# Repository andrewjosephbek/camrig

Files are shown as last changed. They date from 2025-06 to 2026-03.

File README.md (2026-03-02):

# Motorized Camera Tracking Rig

This project implements a compact Camera Motion Platform; integrating custom electronics, embedded firmware, and low-backlash mechanical design. Version 2 is currently in progress (UI firmware is finished, PCB Layout is finished, housing IP)! V1 KiCAD files are for an old version, may be incomplete. 

---

## Version 1: Demo
[Overview Video](https://youtu.be/gTk2HjM0wyA) (1:53)

---

## Version 2: PCB

### 3D:
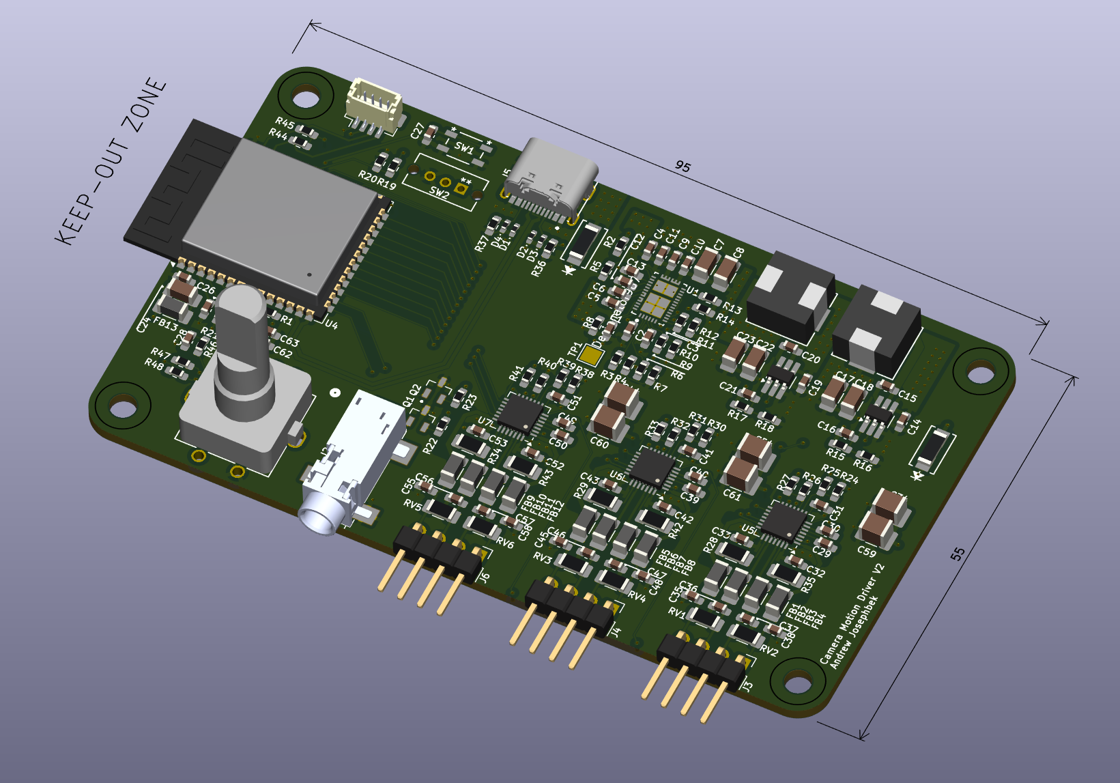
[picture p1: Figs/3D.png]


### Layer 1 (Signal):
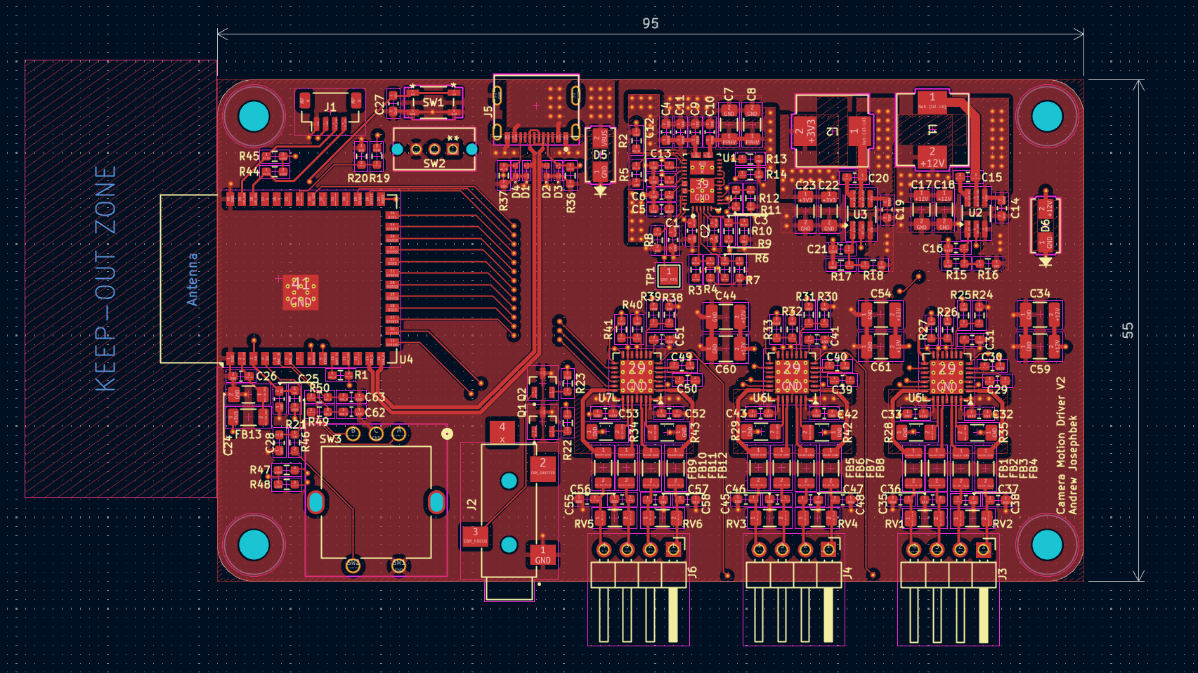
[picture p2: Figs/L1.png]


### Layer 2 (Ground):
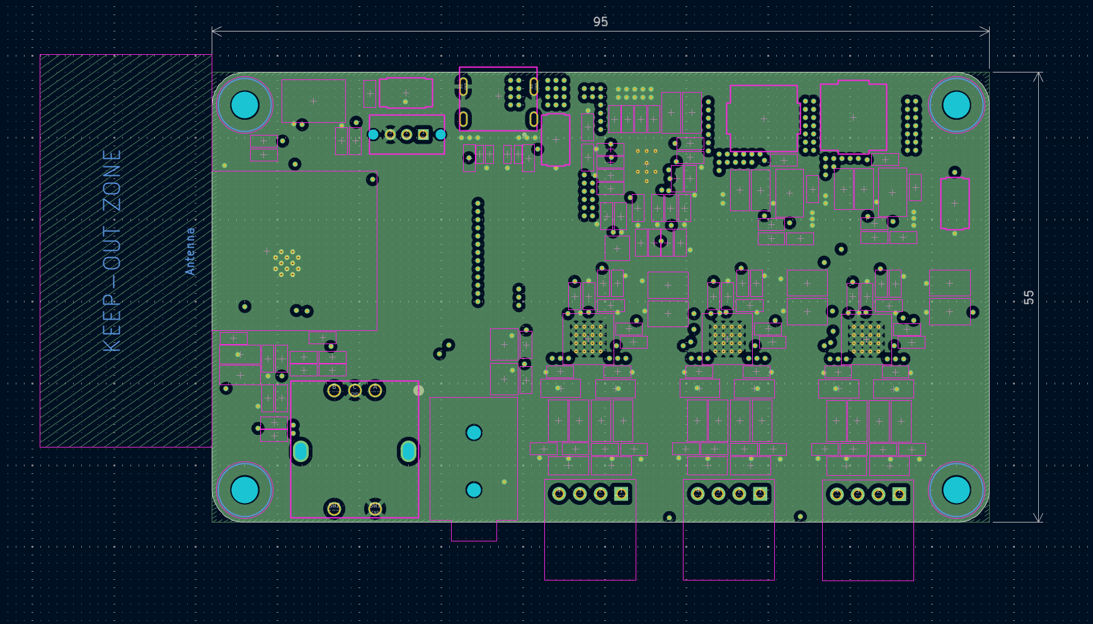
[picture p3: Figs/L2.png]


### Layer 3 (Power):
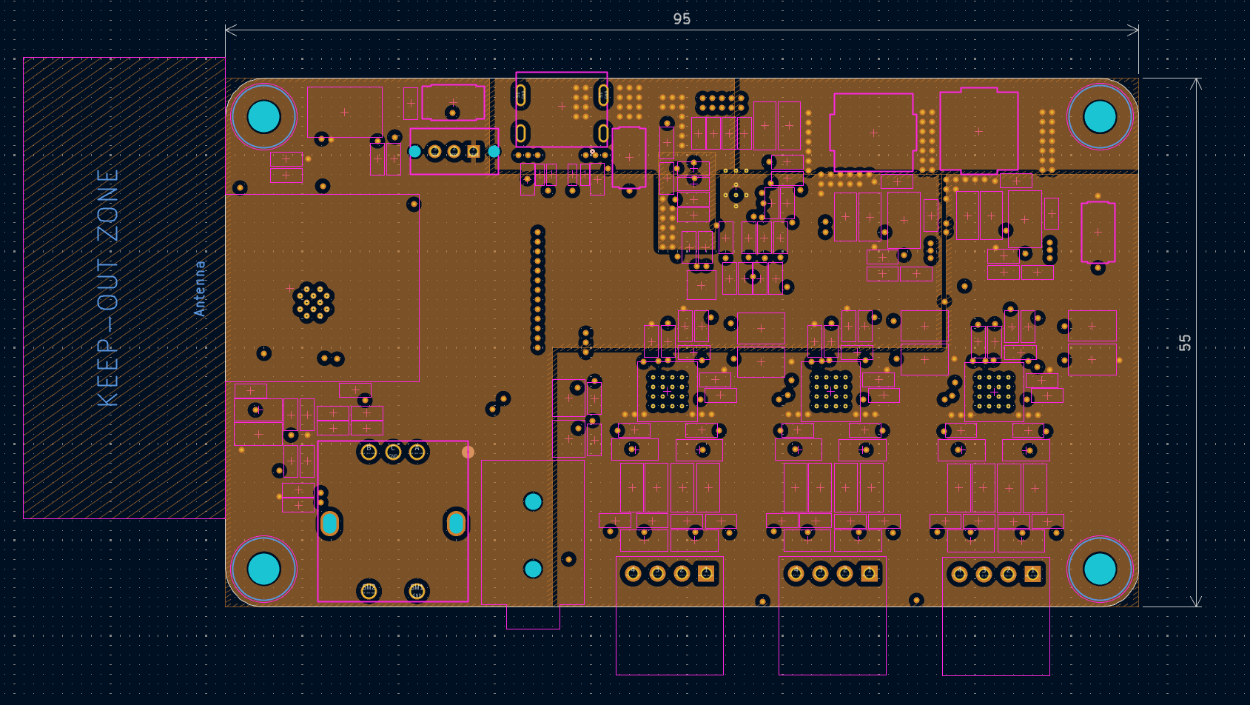
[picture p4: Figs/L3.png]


### Layer 4 (Signal):
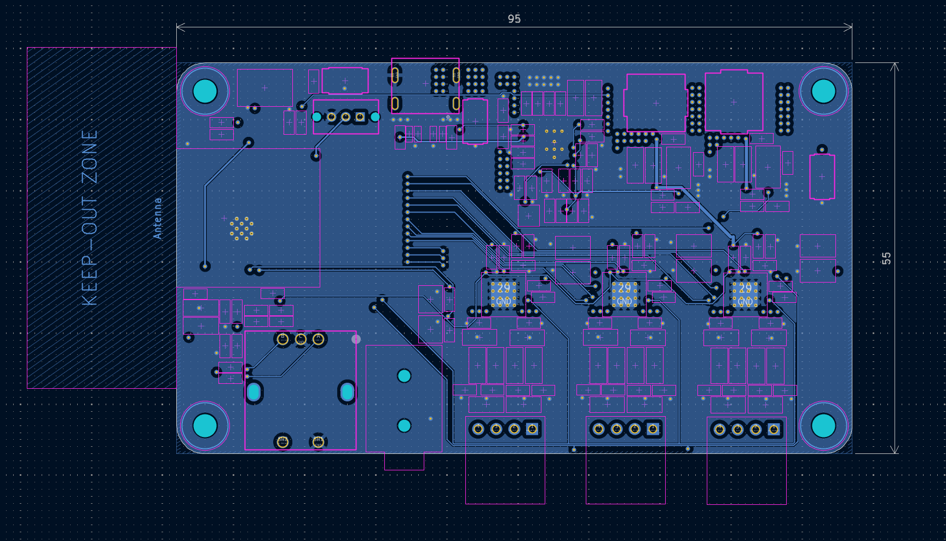
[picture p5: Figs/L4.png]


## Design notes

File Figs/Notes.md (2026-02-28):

https://espressif.github.io/esp32-c3-book-en/chapter_5/5.3/5.3.5.html

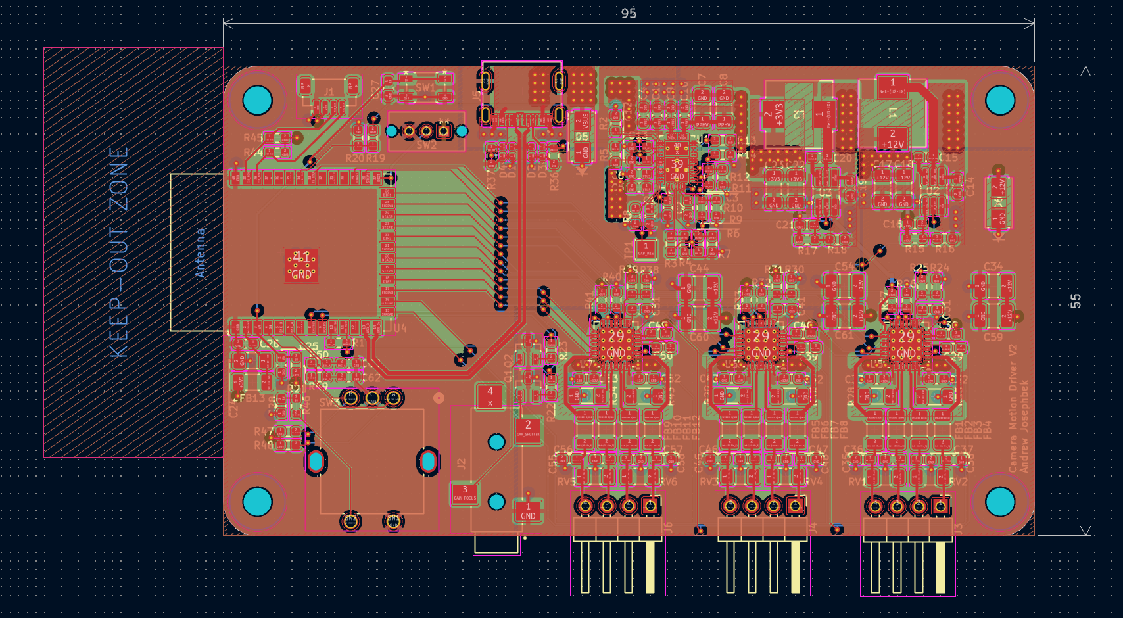
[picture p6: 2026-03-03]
Figs/All Layers.png

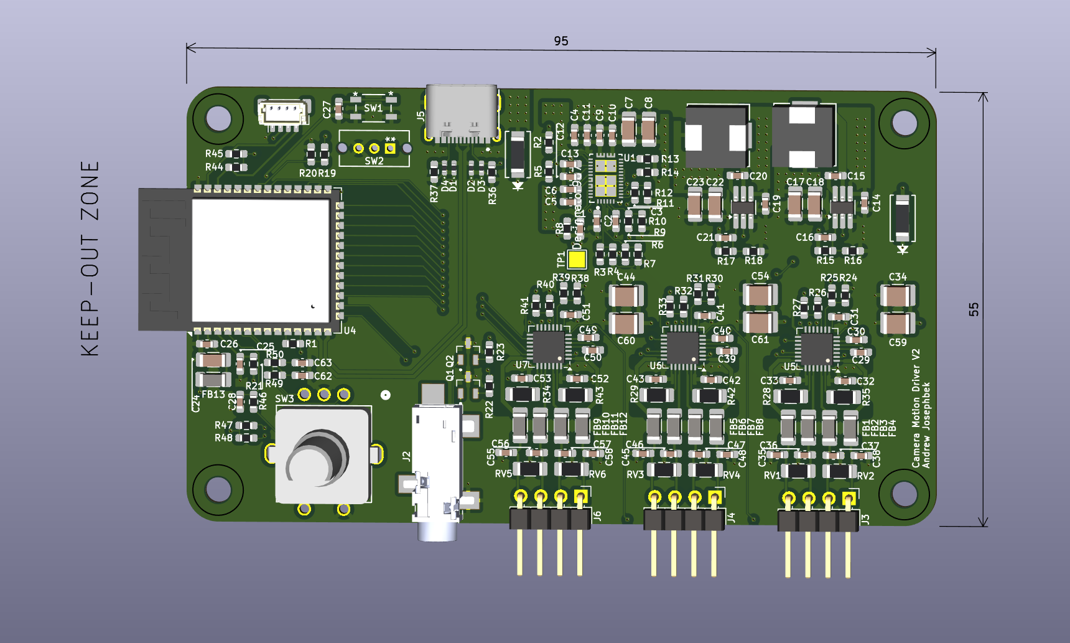
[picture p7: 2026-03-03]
Figs/3D ortho.png

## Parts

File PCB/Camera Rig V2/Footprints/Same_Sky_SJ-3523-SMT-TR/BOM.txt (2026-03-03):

3DX_Same_Sky_Supplier: Same Sky
3DX_Same_Sky_Description: 3.5 mm, Stereo, Right Angle, Surface Mount (SMT), 3 Conductors, 0 Internal Switches, Audio Jack Connector
3DX_Same_Sky_Model Number: SJ-3523-SMT-TR

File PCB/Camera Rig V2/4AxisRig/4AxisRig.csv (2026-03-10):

Reference | Value | Footprint | Part Number | Datasheet | Link | Qty | Description_1
Q1,Q2 | NMOS | 2N7000:SOT95P240X111-3N | 2N7002K | https://www.onsemi.com/download/data-sheet/pdf/2n7002k-d.pdf |  | 2
C1,C2,C10,C14,C19 | 10uF | Capacitor_SMD:C_0603_1608Metric_Pad1.08x0.95mm_HandSolder |  | ~ |  | 5
C3,C4 | 4.7uF | Capacitor_SMD:C_0603_1608Metric_Pad1.08x0.95mm_HandSolder |  | ~ |  | 2
C5,C6,C9,C11 | 0.01uF | Capacitor_SMD:C_0603_1608Metric_Pad1.08x0.95mm_HandSolder |  | ~ |  | 4
C12,C13 | 330pF | Capacitor_SMD:C_0603_1608Metric_Pad1.08x0.95mm_HandSolder |  | ~ |  | 2
C15,C20,C26,C27,C28,C32,C33,C35,C36,C37,C38,C42,C43,C45,C46,C47,C48,C52,C53,C55,C56,C57,C58,C62,C63 | 100nF | Capacitor_SMD:C_0603_1608Metric_Pad1.08x0.95mm_HandSolder |  | ~ |  | 25
C16,C21 | 47pF | Capacitor_SMD:C_0603_1608Metric_Pad1.08x0.95mm_HandSolder |  | ~ |  | 2
C25 | 1uF | Capacitor_SMD:C_0603_1608Metric_Pad1.08x0.95mm_HandSolder |  | ~ |  | 1
C29,C39,C49 | 100nF 16V | Capacitor_SMD:C_0603_1608Metric_Pad1.08x0.95mm_HandSolder |  | ~ |  | 3
C30,C40,C50 | 22nF 50V | Capacitor_SMD:C_0603_1608Metric_Pad1.08x0.95mm_HandSolder |  | ~ |  | 3
C31,C41,C51 | 2.2uF 6.3V | Capacitor_SMD:C_0603_1608Metric_Pad1.08x0.95mm_HandSolder |  | ~ |  | 3
C7,C8,C17,C18,C22,C23,C24 | 22uF | Capacitor_SMD:C_1206_3216Metric_Pad1.33x1.80mm_HandSolder |  | https://mm.digikey.com/Volume0/opasdata/d220001/medias/docus/506/TMK316BBJ226ML-T_SS.pdf |  | 7
C34,C44,C54,C59,C60,C61 | 47uF | Capacitor_SMD:C_1210_3225Metric_Pad1.33x2.70mm_HandSolder |  | https://www.digikey.com/en/products/detail/murata-electronics/GRM32EC81C476KE15L/5027615 |  | 6
J1 | Conn_01x05_Socket | Connector_JST:JST_SH_BM04B-SRSS-TB_1x04-1MP_P1.00mm_Vertical |  | ~ |  | 1
J3,J4,J6 | Motor Connector | Connector_PinHeader_2.54mm:PinHeader_1x04_P2.54mm_Horizontal |  | ~ |  | 3
D1,D2,D3,D4 | ESD441 | Diode_SMD:D_0402_1005Metric_Pad0.77x0.64mm_HandSolder |  | https://www.ti.com/lit/ds/symlink/esd441.pdf?ts=1772263166249 |  | 4
D5 | T4F10A | Diode_SMD:Nexperia_CFP3_SOD-123W |  | DF2B7AFS |  | 1
L2 | 15uH | DR74-150-R:DR74 | DR74-150-R | https://www.eaton.com/content/dam/eaton/products/electronic-components/resources/data-sheet/eaton-dr-high-power-density-high-efficiency-shielded-drum-core-pow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 |  | 1
L1 | 4.7uH | DR74-4R7-R:DR74 | DR74-4R7-R | https://www.eaton.com/content/dam/eaton/products/electronic-components/resources/data-sheet/eaton-dr-high-power-density-high-efficiency-shielded-drum-core-pow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 |  | 1
FB1,FB2,FB3,FB4,FB5,FB6,FB7,FB8,FB9,FB10,FB11,FB12 | 2512065007Y6 | Inductor_SMD:L_1206_3216Metric_Pad1.22x1.90mm_HandSolder |  | https://fair-rite.com/print_product.php?pid=33593 |  | 12
H1,H2,H3,H4 | MountingHole | MountingHole:MountingHole_3.2mm_M3 |  | ~ |  | 4
U5,U6,U7 | TMC2209-LA | Package_DFN_QFN:VQFN-28-1EP_5x5mm_P0.5mm_EP3.7x3.7mm_ThermalVias | TMC2209-LA | https://www.analog.com/media/en/technical-documentation/data-sheets/TMC2209_datasheet_rev1.09.pdf |  | 3
U2,U3 | AN_SY8105 | Package_TO_SOT_SMD:TSOT-23-6_HandSoldering | AN_SY8105 |  |  | 2
SW3 | PEC11L-4120F-S0020 | PEC11L-4120F-S0020:PEC11L-4x20F-Sxxx_BRN |  | PEC11L-4120F-S0020 |  | 1
SW1 | PTS810SJS250SMTRLFS | PTS810SJS250SMTR:SMT_MTRLFS_CNK |  | https://www.ckswitches.com/media/1476/pts810.pdf |  | 1
R1 | 1k | Resistor_SMD:R_0603_1608Metric_Pad0.98x0.95mm_HandSolder |  | ~ |  | 1
R2,R5,R8,R12,R21,R22,R23,R24,R25,R26,R27,R30,R31,R32,R33,R38,R39,R40,R41,R46,R47,R48,R49,R50 | 10k | Resistor_SMD:R_0603_1608Metric_Pad0.98x0.95mm_HandSolder |  | ~ |  | 24
R3,R9,R11 | 191k | Resistor_SMD:R_0603_1608Metric_Pad0.98x0.95mm_HandSolder |  | ~ |  | 3
R4,R10 | 2.5k | Resistor_SMD:R_0603_1608Metric_Pad0.98x0.95mm_HandSolder |  | ~ |  | 2
R6,R7,R17,R19 | 100k | Resistor_SMD:R_0603_1608Metric_Pad0.98x0.95mm_HandSolder |  | ~ |  | 4
R15 | 200k | Resistor_SMD:R_0603_1608Metric_Pad0.98x0.95mm_HandSolder |  | ~ |  | 1
R16 | 10.5k | Resistor_SMD:R_0603_1608Metric_Pad0.98x0.95mm_HandSolder |  | ~ |  | 1
R18 | 22.1k | Resistor_SMD:R_0603_1608Metric_Pad0.98x0.95mm_HandSolder |  | ~ |  | 1
R20 | 19k | Resistor_SMD:R_0603_1608Metric_Pad0.98x0.95mm_HandSolder |  | ~ |  | 1
R36,R37 | 5.1k+-10% | Resistor_SMD:R_0603_1608Metric_Pad0.98x0.95mm_HandSolder |  | ~ |  | 2
R44,R45 | 4.7k | Resistor_SMD:R_0603_1608Metric_Pad0.98x0.95mm_HandSolder |  | ~ |  | 2
R28,R29,R34,R35,R42,R43 | 0.68 | Resistor_SMD:R_1206_3216Metric_Pad1.30x1.75mm_HandSolder |  | ~ |  | 6
RV1,RV2,RV3,RV4,RV5,RV6 | CG0603MLA-18KE | Resistor_SMD:R_1206_3216Metric_Pad1.30x1.75mm_HandSolder |  | ~ |  | 6
U4 | ESP32-S3-WROOM-1 | RF_Module:ESP32-S3-WROOM-1 | ESP32-S3-WROOM-1 | https://www.espressif.com/sites/default/files/documentation/esp32-s3-wroom-1_wroom-1u_datasheet_en.pdf |  | 1
J2 | SJ-3524-SMT | SJ-3524-SMT:CUI_SJ-3524-SMT |  | https://www.sameskydevices.com/product/resource/sj-352x-smt.pdf |  | 1 | 3.5 mm, Stereo, Right Angle, Surface Mount (SMT), 3 Conductors, 1 Internal Switch, Audio Jack Connector
SW2 | SW_SPDT | SS-12D07-VG 4 NS GA PA:SS12D07_CNK |  | https://mm.digikey.com/Volume0/opasdata/d220001/medias/docus/580/SS-12D07-VG_GA_PA.pdf |  | 1
TP7 | TestPoint | TestPoint:TestPoint_Keystone_5000-5004_Miniature |  | ~ |  | 1
TP1,TP2,TP3,TP4,TP5,TP6,TP8 | TestPoint | TestPoint:TestPoint_Pad_1.0x1.0mm |  | ~ |  | 7
U1 | TPS25730DREFR | TPS25730DREFR:REF0038A-MFG | TPS25730DREFR | https://www.ti.com/lit/gpn/tps25730 |  | 1
J5 | USB_C_Receptacle_USB2.0_16P | USB_C_Receptacle_USB2.0_14P:CONN_8p94X6p5X3p16_12L_GCC |  | https://www.usb.org/sites/default/files/documents/usb_type-c.zip |  | 1

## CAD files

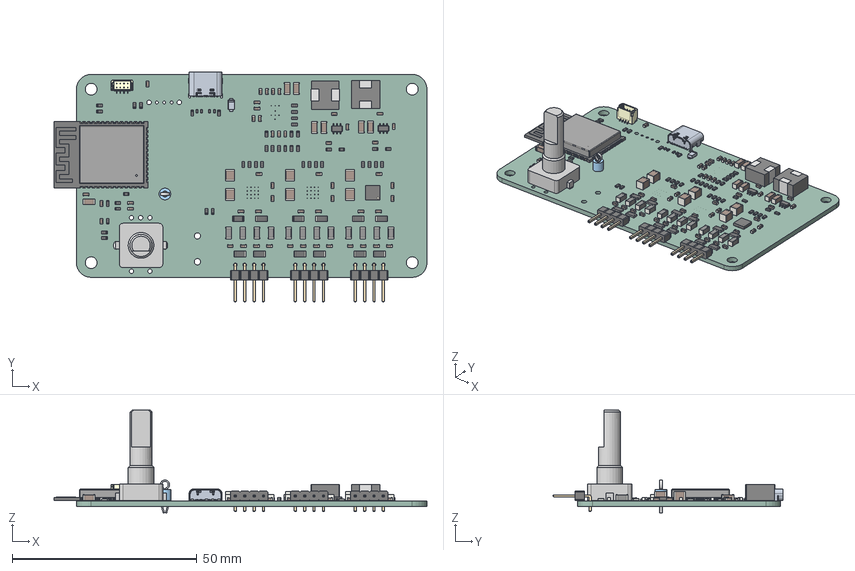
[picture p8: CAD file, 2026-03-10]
PCB/Camera Rig V2/4AxisRig/4AxisRig.step
101.1 x 62.3 x 27.8 mm
C_1210_3225Metric x 6
L_1206_3216Metric x 12
C_0603_1608Metric x 50
C_1206_3216Metric x 7
R_0402_1005Metric x 4
R_0603_1608Metric x 44
R_1206_3216Metric x 12
TestPoint_Keystone_5005-5009_Compact
4AxisRig 1.28.1
DR74 x 2
QFN-32-1EP_4x4mm_P0.4mm_EP2.65x2.65mm
PinHeader_1x04_P2.54mm_Horizontal x 3
TSOT-23-6 x 2
BM04B-SRSS-TB--3DModel-STEP-1
Rot Enc v1
ESP32-S3-WROOM-1
4AxisRig_PCB

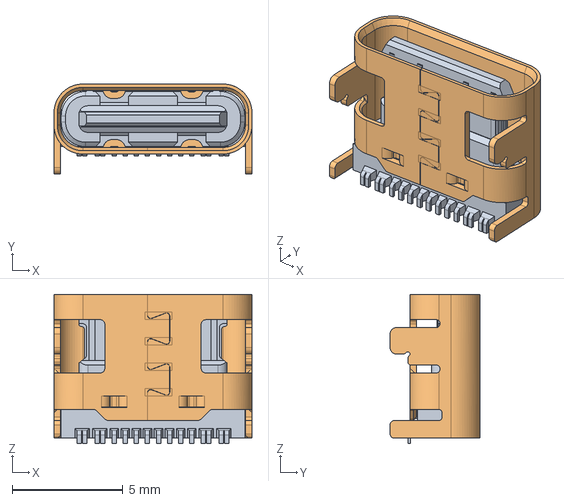
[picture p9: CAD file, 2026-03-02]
PCB/Camera Rig V2/Footprints/179536900-3-usb4215-03-a/usb4215-03-a.stp
8.94 x 4.06 x 6.75 mm

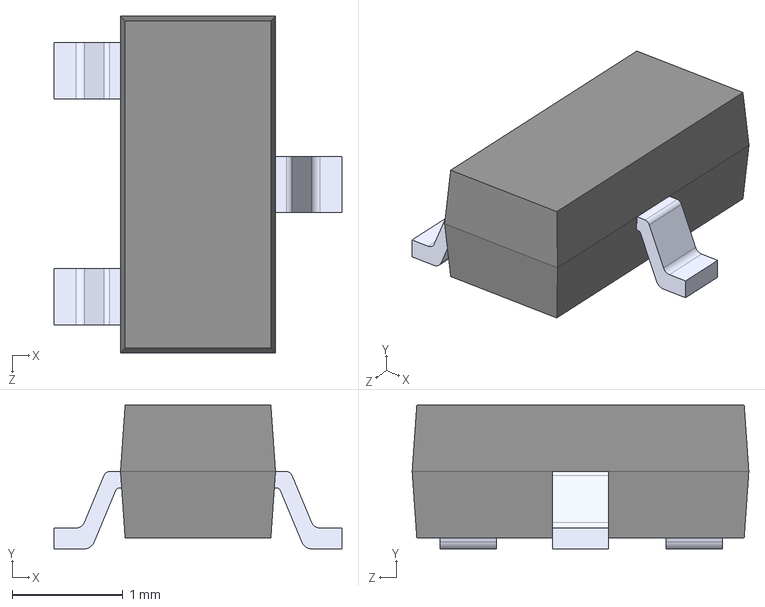
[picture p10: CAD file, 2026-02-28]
PCB/Camera Rig V2/Footprints/2N7002KT7G/2N7002KT7G.step
2.60 x 1.30 x 3.04 mm

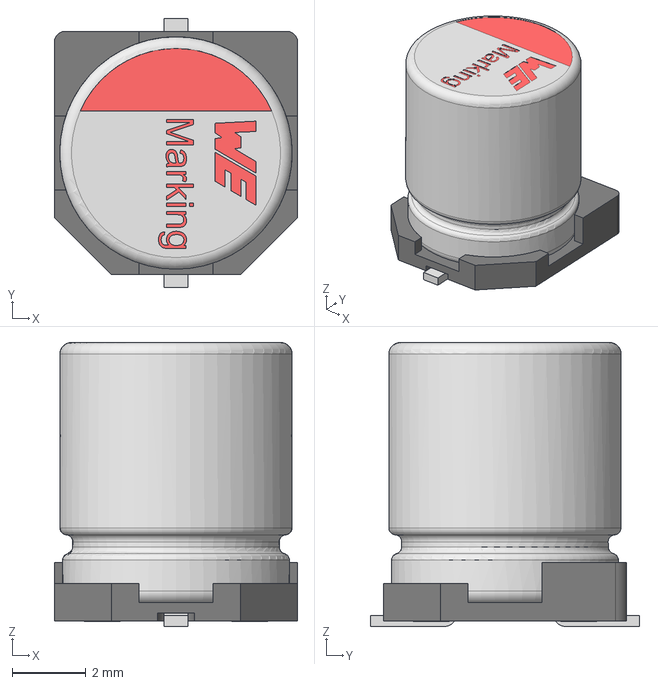
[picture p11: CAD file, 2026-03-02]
PCB/Camera Rig V2/Footprints/Download_STP_86508xx450xx+(rev1)/Download_STP_86508xx450xx+%28rev1%29.stp
6.60 x 7.30 x 7.70 mm
capicitor_6.3x7.7x2.2
Base_Φ6_3Capacitor

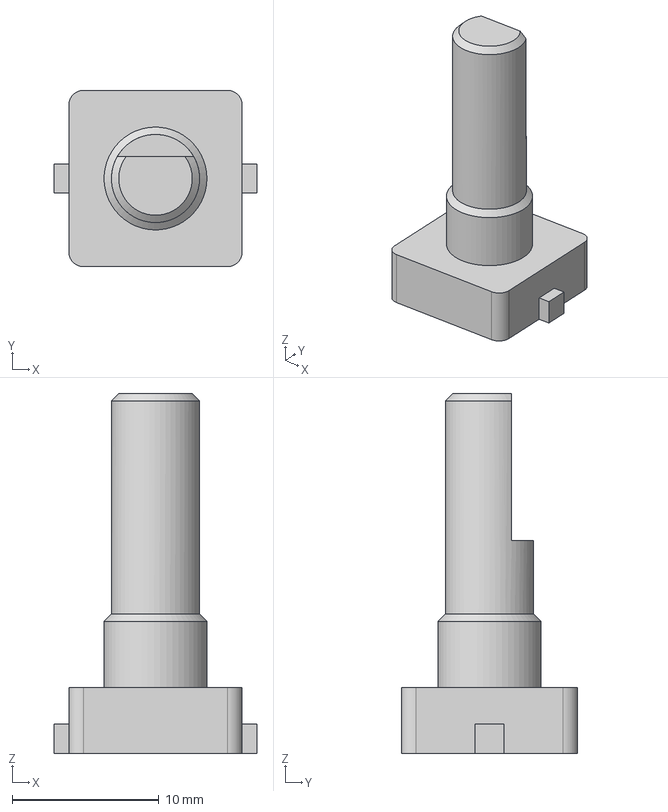
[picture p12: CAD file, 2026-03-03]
PCB/Camera Rig V2/Footprints/Rot Enc v1.step
13.8 x 12.0 x 24.5 mm

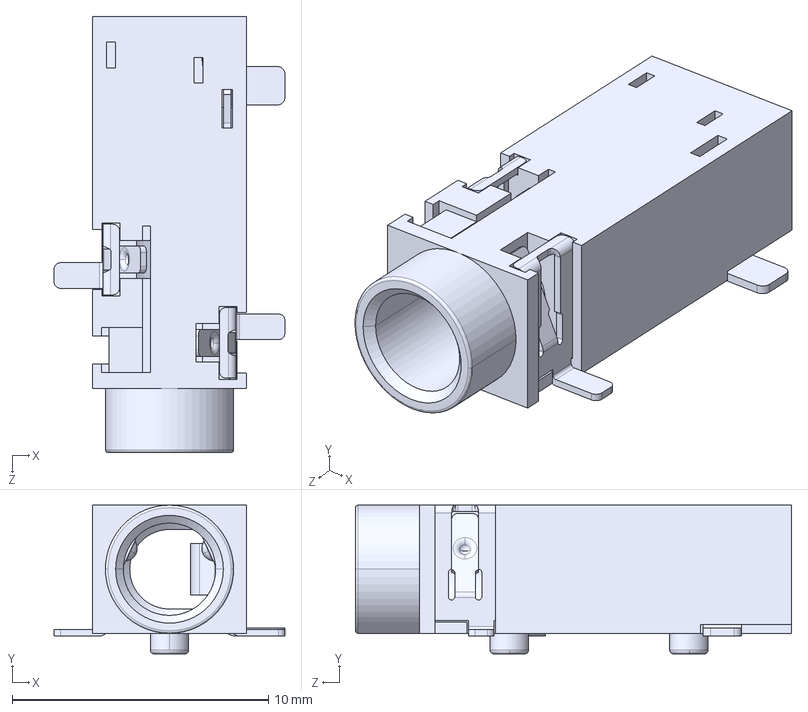
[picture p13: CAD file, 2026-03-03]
PCB/Camera Rig V2/Footprints/Same_Sky_SJ-3523-SMT-TR/Same_Sky_SJ-3523-SMT-TR.step
9.00 x 5.80 x 17.0 mm

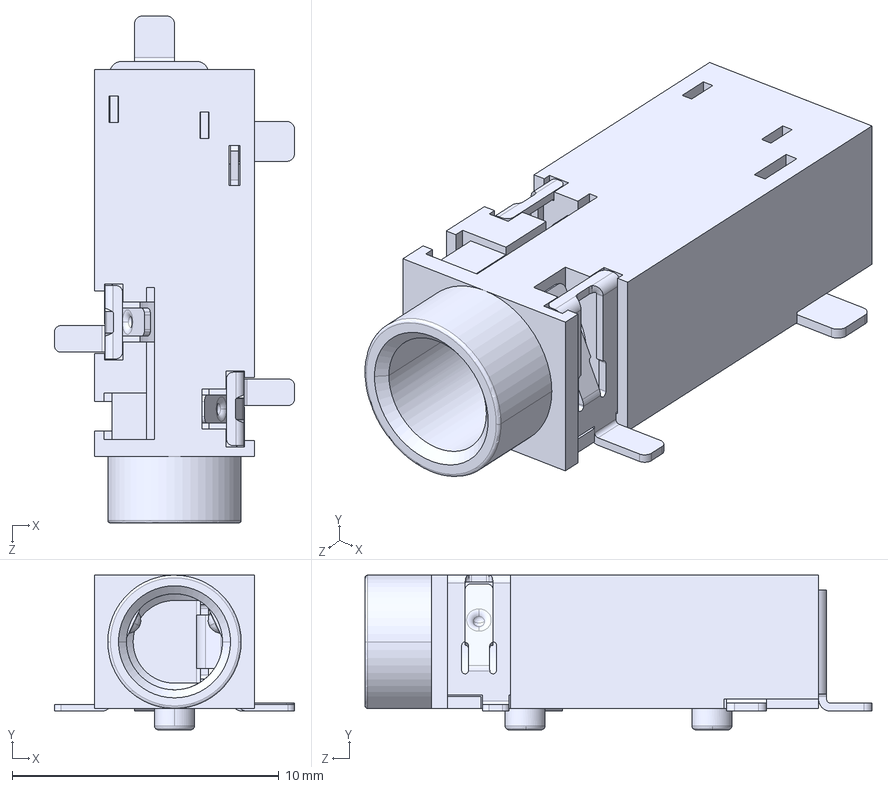
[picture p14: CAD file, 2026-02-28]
PCB/Camera Rig V2/Footprints/SJ-3524-SMT/SJ-3524-SMT.step
9.00 x 5.80 x 19.0 mm

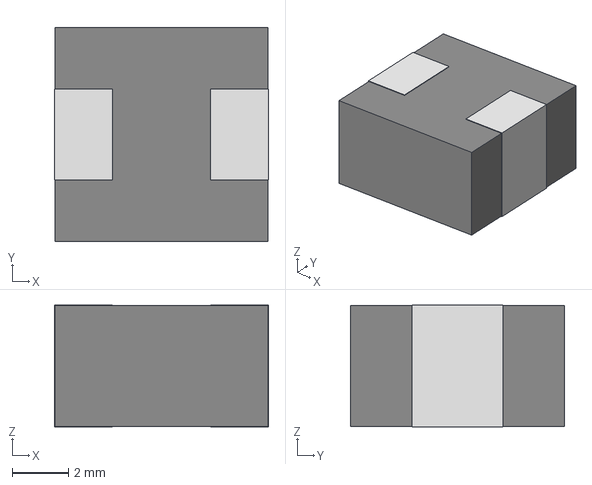
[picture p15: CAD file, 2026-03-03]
PCB/Camera Rig V2/Footprints/ul_DR74-150-R (1)/DR74.step
7.62 x 7.62 x 4.34 mm

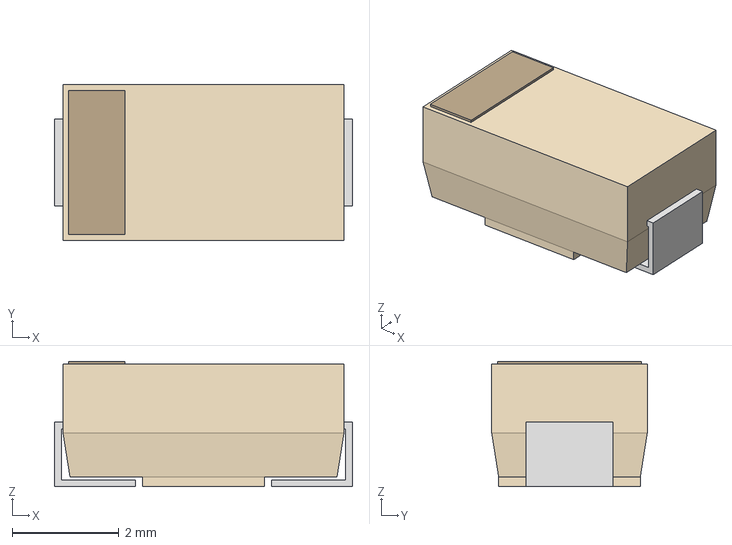
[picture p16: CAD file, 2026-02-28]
PCB/Camera Rig V2/Footprints/ul_SMAJ10CA-13-F/SMA_DIO.step
5.59 x 2.92 x 2.35 mm

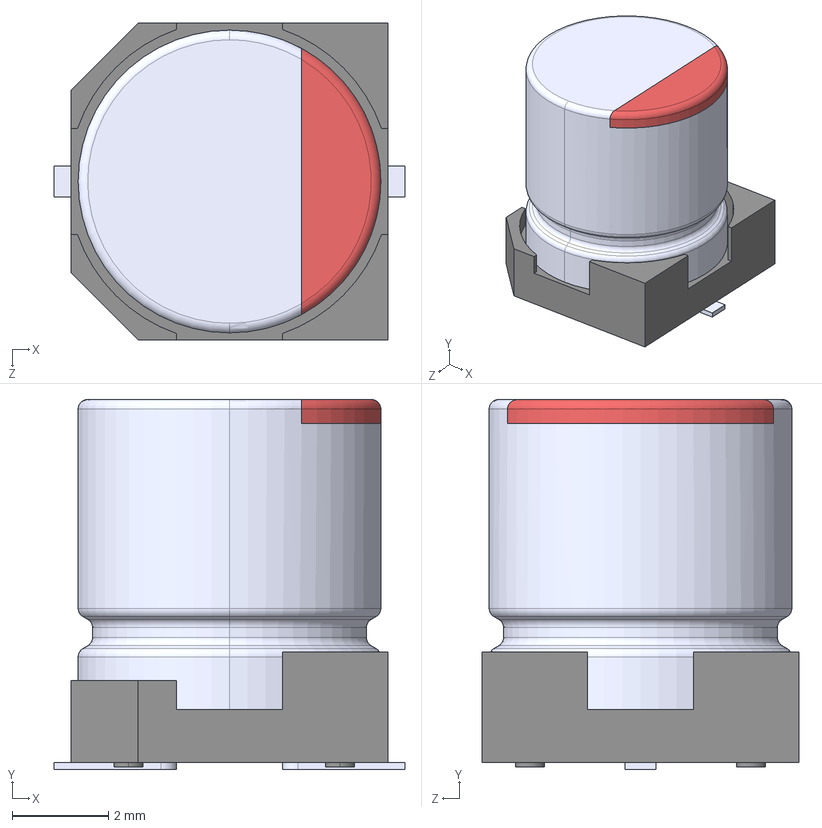
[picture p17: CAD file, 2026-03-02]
PCB/Camera Rig V2/Footprints/WCAP-ASLI_6.3X7.7/WCAP-ASLI_6.3X7.7.step
7.30 x 7.70 x 6.60 mm

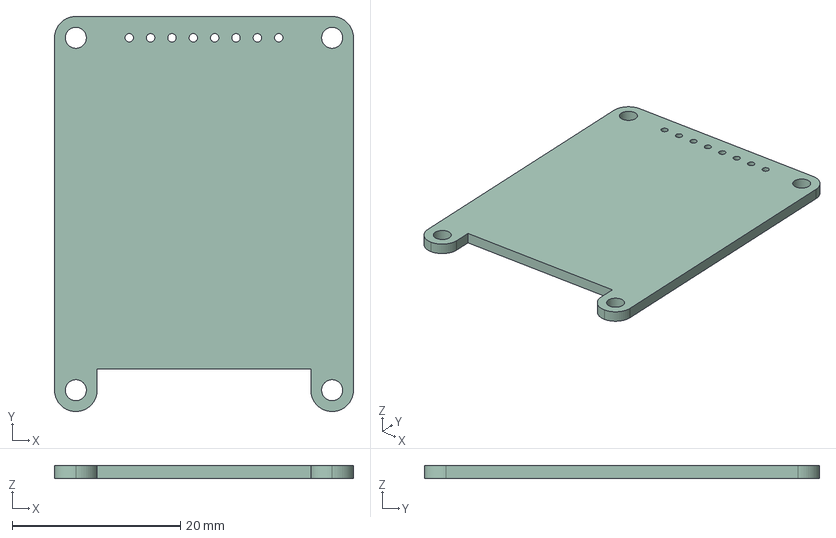
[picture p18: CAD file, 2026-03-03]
PCB/Camera Rig V2/Peripherals/Adafruit Grayscale 1.5-inch 128x128 OLED.step
35.6 x 47.0 x 1.51 mm

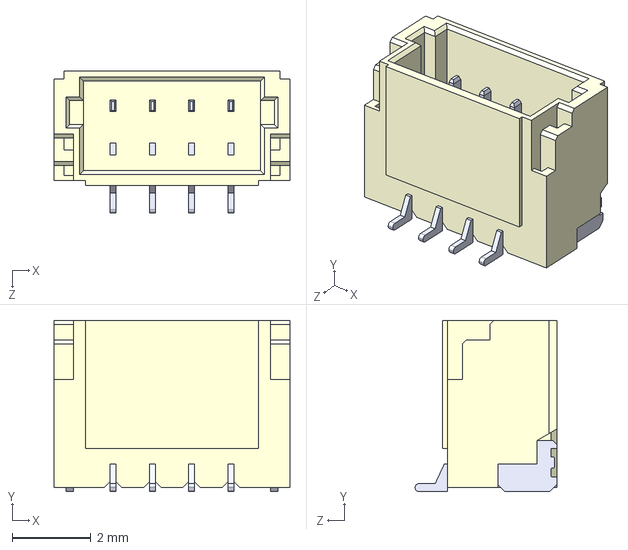
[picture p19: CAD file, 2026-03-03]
PCB/Camera Rig V2/Footprints/BM04B-SRSS-TB--3DModel-STEP-1.STEP
6.00 x 4.35 x 3.60 mm

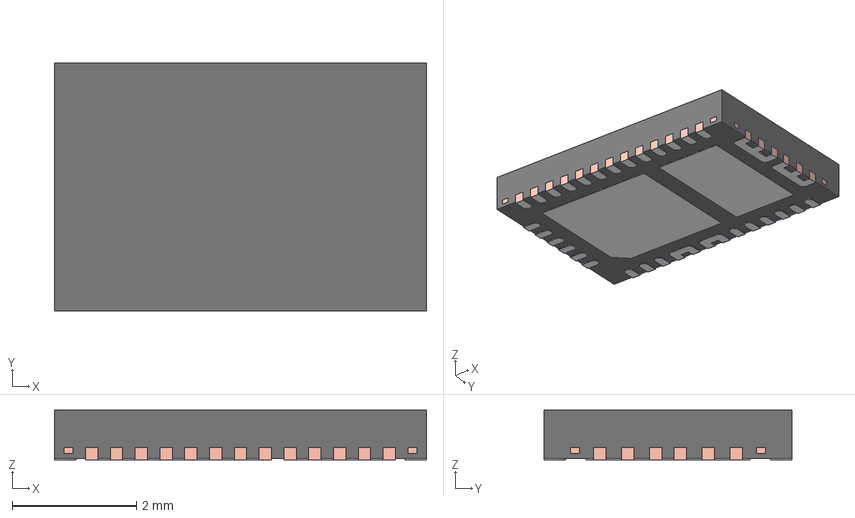
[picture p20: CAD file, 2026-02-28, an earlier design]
PCB/Camera Rig V2/Footprints/ul_TPS25730DREFR (1)/REF0038A.stp
6.00 x 4.00 x 0.8 mm
BODY-QFN
FRAME-REF0038A
PIN1-ID

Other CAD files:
3D/Cradle v13.f3z
3D/Knob v7.f3d

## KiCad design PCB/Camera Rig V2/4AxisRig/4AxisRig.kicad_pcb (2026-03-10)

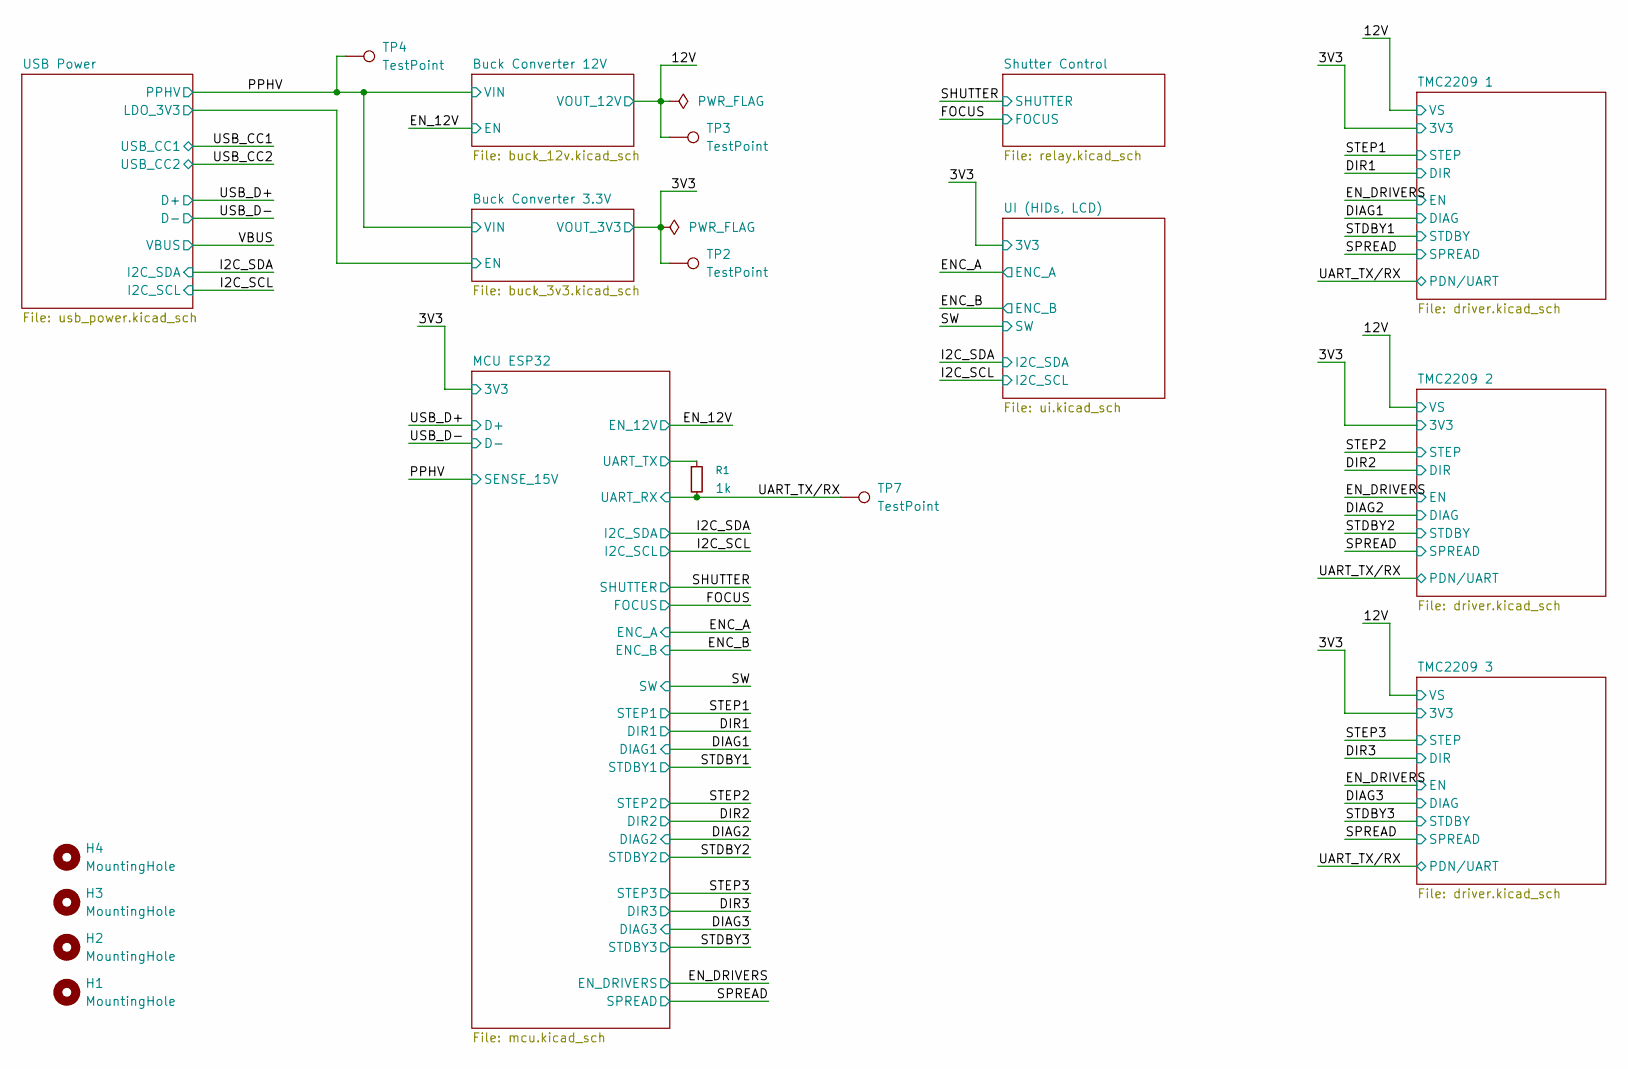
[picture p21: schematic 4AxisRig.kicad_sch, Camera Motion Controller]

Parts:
H1, H2, H3, H4: MountingHole; MountingHole_3.2mm_M3
R1: 1k; R_0603_1608Metric_Pad0.98x0.95mm_HandSolder
TP2, TP3, TP4: TestPoint; TestPoint_Pad_1.0x1.0mm
TP7: TestPoint; TestPoint_Keystone_5000-5004_Miniature

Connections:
/3V3: TP2.1; also elsewhere on the board
/12V: TP3.1; also elsewhere on the board
/MCU ESP32/UART_TX: R1.1; also elsewhere on the board
/PPHV: TP4.1; also elsewhere on the board
/UART_TX/RX: R1.2, TP7.1; also elsewhere on the board

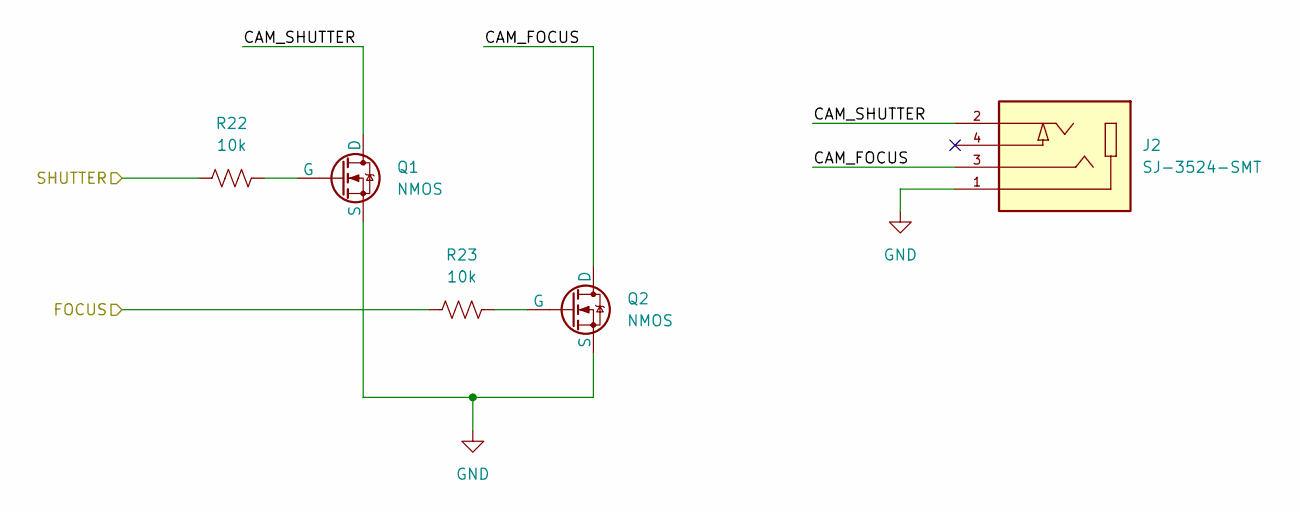
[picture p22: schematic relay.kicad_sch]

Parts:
J2: SJ-3524-SMT; CUI_SJ-3524-SMT; PARTREV 1.03; DigiKey_Part_Number CP-3524SJCT-ND
Q1, Q2: NMOS; SOT95P240X111-3N; Part Number 2N7002K
R22, R23: 10k; R_0603_1608Metric_Pad0.98x0.95mm_HandSolder

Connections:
/FOCUS: R23.1; also elsewhere on the board
/SHUTTER: R22.1; also elsewhere on the board
/Shutter Control/CAM_FOCUS: J2.3, Q2.1 (D)
/Shutter Control/CAM_SHUTTER: J2.2, Q1.1 (D)
GND: J2.1, Q1.3 (S), Q2.3 (S); also elsewhere on the board
unnamed: Q1.2 (G), R22.2
unnamed: Q2.2 (G), R23.2

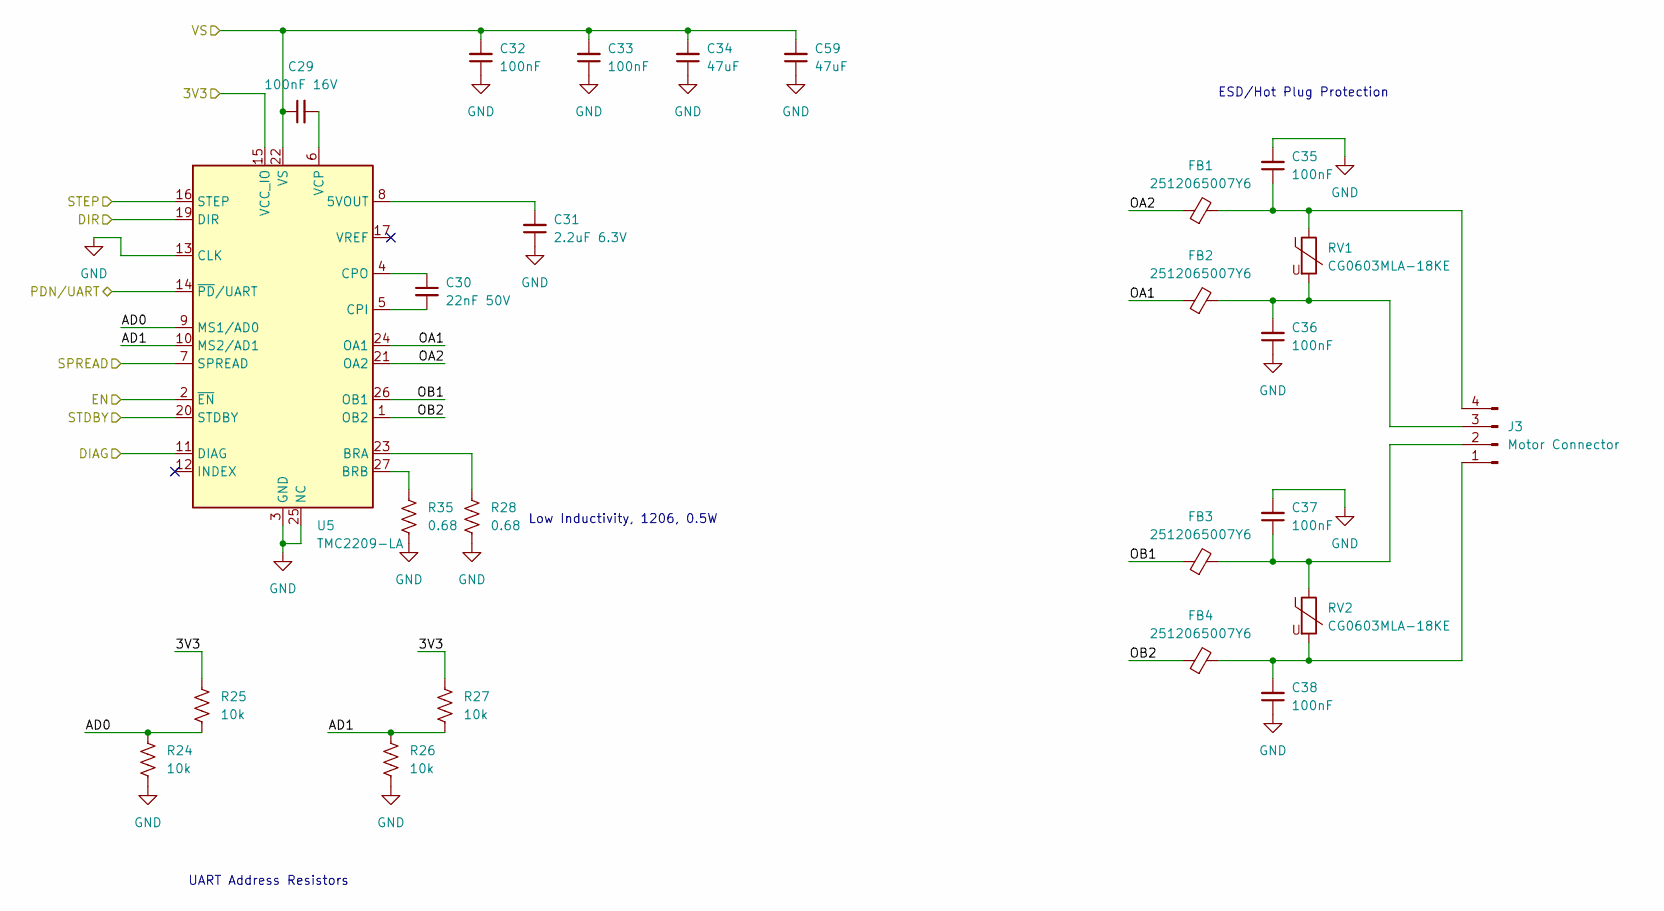
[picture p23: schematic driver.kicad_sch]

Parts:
C29: 100nF 16V; C_0603_1608Metric_Pad1.08x0.95mm_HandSolder
C30: 22nF 50V; C_0603_1608Metric_Pad1.08x0.95mm_HandSolder
C31: 2.2uF 6.3V; C_0603_1608Metric_Pad1.08x0.95mm_HandSolder
C32, C33, C35, C36, C37, C38: 100nF; C_0603_1608Metric_Pad1.08x0.95mm_HandSolder
C34, C59: 47uF; C_1210_3225Metric_Pad1.33x2.70mm_HandSolder
FB1, FB2, FB3, FB4: 2512065007Y6; L_1206_3216Metric_Pad1.22x1.90mm_HandSolder
J3: Motor Connector; PinHeader_1x04_P2.54mm_Horizontal
R24, R25, R26, R27: 10k; R_0603_1608Metric_Pad0.98x0.95mm_HandSolder
R28, R35: 0.68; R_1206_3216Metric_Pad1.30x1.75mm_HandSolder
RV1, RV2: CG0603MLA-18KE; R_1206_3216Metric_Pad1.30x1.75mm_HandSolder
U5: TMC2209-LA; VQFN-28-1EP_5x5mm_P0.5mm_EP3.7x3.7mm_ThermalVias; Part Number TMC2209-LA

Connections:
/3V3: R25.2, R27.2, U5.15 (VCC_IO); also elsewhere on the board
/12V: C29.1, C32.2, C33.2, C34.2, C59.2, U5.22 (VS), U5.28 (VS); also elsewhere on the board
/DIAG1: U5.11 (DIAG); also elsewhere on the board
/DIR1: U5.19 (DIR); also elsewhere on the board
/EN_DRIVERS: U5.2 (~EN); also elsewhere on the board
/SPREAD: U5.7 (SPREAD); also elsewhere on the board
/STDBY1: U5.20 (STDBY); also elsewhere on the board
/STEP1: U5.16 (STEP); also elsewhere on the board
/TMC2209 1/AD0: R24.2, R25.1, U5.9 (MS1/AD0)
/TMC2209 1/AD1: R26.2, R27.1, U5.10 (MS2/AD1)
/TMC2209 1/OA1: FB2.1, U5.24 (OA1)
/TMC2209 1/OA2: FB1.1, U5.21 (OA2)
/TMC2209 1/OB1: FB3.1, U5.26 (OB1)
/TMC2209 1/OB2: FB4.1, U5.1 (OB2)
/UART_TX/RX: U5.14 (~PD/UART); also elsewhere on the board
GND: C31.1, C32.1, C33.1, C34.1, C35.2, C36.1, C37.2, C38.1, C59.1, R24.1, R26.1, R28.1, R35.1, U5.3 (GND), U5.13 (CLK), U5.18 (GND), U5.25 (NC), U5.29 (GND); also elsewhere on the board
unnamed: C38.2, FB4.2, J3.1, RV2.2
unnamed: C37.1, FB3.2, J3.2, RV2.1
unnamed: C36.2, FB2.2, J3.3, RV1.2
unnamed: C35.1, FB1.2, J3.4, RV1.1
unnamed: C31.2, U5.8 (5VOUT)
unnamed: R28.2, U5.23 (BRA)
unnamed: R35.2, U5.27 (BRB)
unnamed: C30.2, U5.5 (CPI)
unnamed: C30.1, U5.4 (CPO)
unnamed: C29.2, U5.6 (VCP)

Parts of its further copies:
C39, C49: 100nF 16V; C_0603_1608Metric_Pad1.08x0.95mm_HandSolder
C40, C50: 22nF 50V; C_0603_1608Metric_Pad1.08x0.95mm_HandSolder
C41, C51: 2.2uF 6.3V; C_0603_1608Metric_Pad1.08x0.95mm_HandSolder
C42, C43, C45, C46, C47, C48, C52, C53, C55, C56, C57, C58: 100nF; C_0603_1608Metric_Pad1.08x0.95mm_HandSolder
C44, C54, C60, C61: 47uF; C_1210_3225Metric_Pad1.33x2.70mm_HandSolder
FB5, FB6, FB7, FB8, FB9, FB10, FB11, FB12: 2512065007Y6; L_1206_3216Metric_Pad1.22x1.90mm_HandSolder
J4, J6: Motor Connector; PinHeader_1x04_P2.54mm_Horizontal
R29, R34, R42, R43: 0.68; R_1206_3216Metric_Pad1.30x1.75mm_HandSolder
R30, R31, R32, R33, R38, R39, R40, R41: 10k; R_0603_1608Metric_Pad0.98x0.95mm_HandSolder
RV3, RV4, RV5, RV6: CG0603MLA-18KE; R_1206_3216Metric_Pad1.30x1.75mm_HandSolder
U6, U7: TMC2209-LA; VQFN-28-1EP_5x5mm_P0.5mm_EP3.7x3.7mm_ThermalVias; Part Number TMC2209-LA

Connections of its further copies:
/3V3: R31.2, R33.2, R39.2, R41.2, U6.15 (VCC_IO), U7.15 (VCC_IO); also elsewhere on the board
/12V: C39.1, C42.2, C43.2, C44.2, C49.1, C52.2, C53.2, C54.2, C60.2, C61.2, U6.22 (VS), U6.28 (VS), U7.22 (VS), U7.28 (VS); also elsewhere on the board
/DIAG2: U6.11 (DIAG); also elsewhere on the board
/DIAG3: U7.11 (DIAG); also elsewhere on the board
/DIR2: U6.19 (DIR); also elsewhere on the board
/DIR3: U7.19 (DIR); also elsewhere on the board
/EN_DRIVERS: U6.2 (~EN), U7.2 (~EN); also elsewhere on the board
/SPREAD: U6.7 (SPREAD), U7.7 (SPREAD); also elsewhere on the board
/STDBY2: U6.20 (STDBY); also elsewhere on the board
/STDBY3: U7.20 (STDBY); also elsewhere on the board
/STEP2: U6.16 (STEP); also elsewhere on the board
/STEP3: U7.16 (STEP); also elsewhere on the board
/TMC2209 2/AD0: R30.2, R31.1, U6.9 (MS1/AD0)
/TMC2209 2/AD1: R32.2, R33.1, U6.10 (MS2/AD1)
/TMC2209 2/OA1: FB6.1, U6.24 (OA1)
/TMC2209 2/OA2: FB5.1, U6.21 (OA2)
/TMC2209 2/OB1: FB7.1, U6.26 (OB1)
/TMC2209 2/OB2: FB8.1, U6.1 (OB2)
/TMC2209 3/AD0: R38.2, R39.1, U7.9 (MS1/AD0)
/TMC2209 3/AD1: R40.2, R41.1, U7.10 (MS2/AD1)
/TMC2209 3/OA1: FB10.1, U7.24 (OA1)
/TMC2209 3/OA2: FB9.1, U7.21 (OA2)
/TMC2209 3/OB1: FB11.1, U7.26 (OB1)
/TMC2209 3/OB2: FB12.1, U7.1 (OB2)
/UART_TX/RX: U6.14 (~PD/UART), U7.14 (~PD/UART); also elsewhere on the board
GND: C41.1, C42.1, C43.1, C44.1, C45.2, C46.1, C47.2, C48.1, C51.1, C52.1, C53.1, C54.1, C55.2, C56.1, C57.2, C58.1, C60.1, C61.1, R29.1, R30.1, R32.1, R34.1, R38.1, R40.1, R42.1, R43.1, U6.3 (GND), U6.13 (CLK), U6.18 (GND), U6.25 (NC), U6.29 (GND), U7.3 (GND), U7.13 (CLK), U7.18 (GND), U7.25 (NC), U7.29 (GND); also elsewhere on the board
unnamed: C48.2, FB8.2, J4.1, RV4.2
unnamed: C47.1, FB7.2, J4.2, RV4.1
unnamed: C46.2, FB6.2, J4.3, RV3.2
unnamed: C45.1, FB5.2, J4.4, RV3.1
unnamed: C58.2, FB12.2, J6.1, RV6.2
unnamed: C57.1, FB11.2, J6.2, RV6.1
unnamed: C56.2, FB10.2, J6.3, RV5.2
unnamed: C55.1, FB9.2, J6.4, RV5.1
unnamed: C41.2, U6.8 (5VOUT)
unnamed: R29.2, U6.23 (BRA)
unnamed: R42.2, U6.27 (BRB)
unnamed: C40.2, U6.5 (CPI)
unnamed: C40.1, U6.4 (CPO)
unnamed: C39.2, U6.6 (VCP)
unnamed: C51.2, U7.8 (5VOUT)
unnamed: R34.2, U7.23 (BRA)
unnamed: R43.2, U7.27 (BRB)
unnamed: C50.2, U7.5 (CPI)
unnamed: C50.1, U7.4 (CPO)
unnamed: C49.2, U7.6 (VCP)

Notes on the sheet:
UART Address Resistors
ESD/Hot Plug Protection
Low Inductivity, 1206, 0.5W

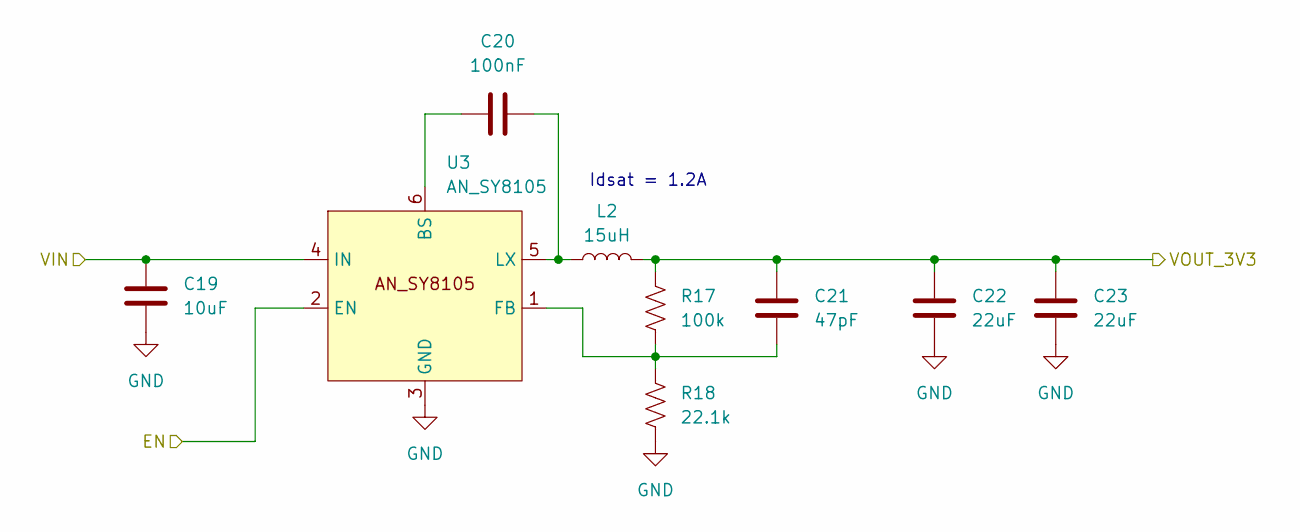
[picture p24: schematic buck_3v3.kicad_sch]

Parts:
C19: 10uF; C_0603_1608Metric_Pad1.08x0.95mm_HandSolder
C20: 100nF; C_0603_1608Metric_Pad1.08x0.95mm_HandSolder
C21: 47pF; C_0603_1608Metric_Pad1.08x0.95mm_HandSolder
C22, C23: 22uF; C_1206_3216Metric_Pad1.33x1.80mm_HandSolder
L2: 15uH; DR74; Part Number DR74-150-R
R17: 100k; R_0603_1608Metric_Pad0.98x0.95mm_HandSolder
R18: 22.1k; R_0603_1608Metric_Pad0.98x0.95mm_HandSolder
U3: AN_SY8105; TSOT-23-6_HandSoldering; Part Number AN_SY8105

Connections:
/3V3: C21.1, C22.1, C23.1, L2.2, R17.1; also elsewhere on the board
/PPHV: C19.1, U3.4 (IN); also elsewhere on the board
/USB Power/LDO_3V3: U3.2 (EN); also elsewhere on the board
GND: C19.2, C22.2, C23.2, R18.2, U3.3 (GND); also elsewhere on the board
unnamed: C20.2, U3.6 (BS)
unnamed: C21.2, R17.2, R18.1, U3.1 (FB)
unnamed: C20.1, L2.1, U3.5 (LX)

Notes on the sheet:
Idsat = 1.2A

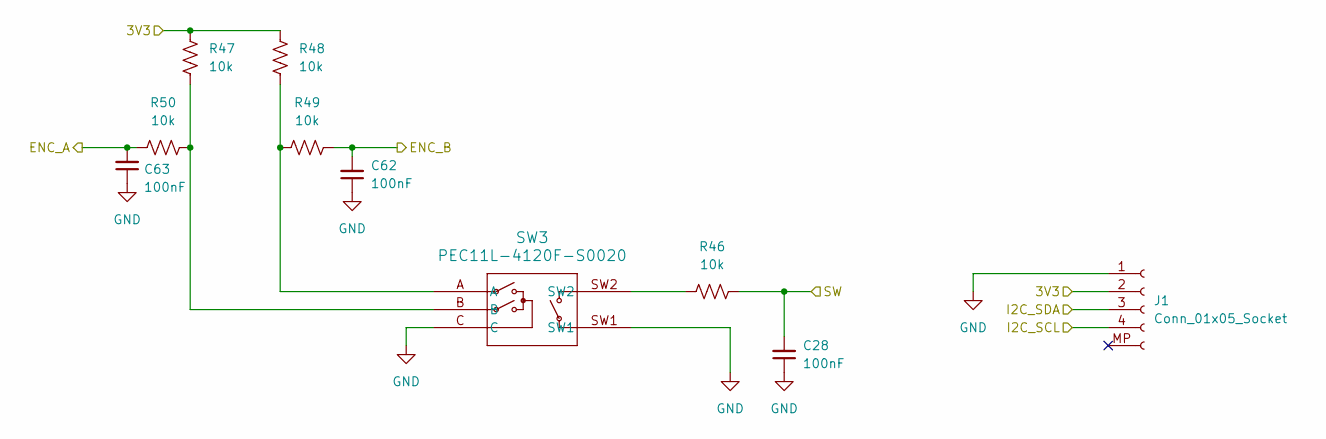
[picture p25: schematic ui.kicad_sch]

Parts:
C28, C62, C63: 100nF; C_0603_1608Metric_Pad1.08x0.95mm_HandSolder
J1: Conn_01x05_Socket; JST_SH_BM04B-SRSS-TB_1x04-1MP_P1.00mm_Vertical
R46, R47, R48, R49, R50: 10k; R_0603_1608Metric_Pad0.98x0.95mm_HandSolder
SW3: PEC11L-4120F-S0020; PEC11L-4x20F-Sxxx_BRN

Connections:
/3V3: J1.2, R47.1, R48.1; also elsewhere on the board
/ENC_A: C63.2, R50.1; also elsewhere on the board
/ENC_B: C62.2, R49.2; also elsewhere on the board
/I2C_SCL: J1.4; also elsewhere on the board
/I2C_SDA: J1.3; also elsewhere on the board
/SW: C28.2, R46.1; also elsewhere on the board
GND: C28.1, C62.1, C63.1, J1.1, SW3.C, SW3.SW1; also elsewhere on the board
unnamed: R46.2, SW3.SW2
unnamed: R47.2, R50.2, SW3.B
unnamed: R48.2, R49.1, SW3.A

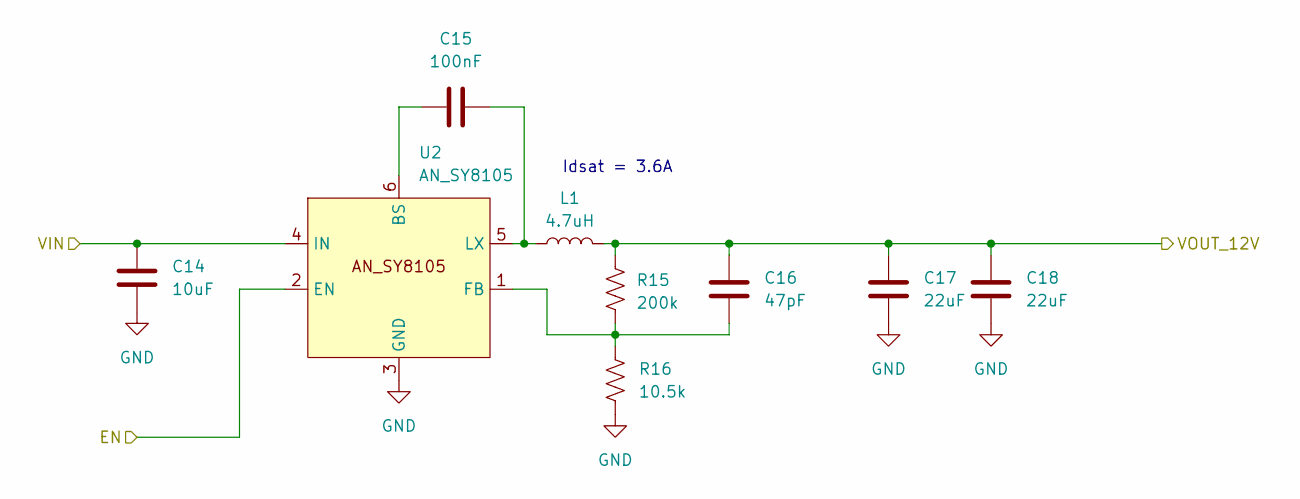
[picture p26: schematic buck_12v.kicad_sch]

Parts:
C14: 10uF; C_0603_1608Metric_Pad1.08x0.95mm_HandSolder
C15: 100nF; C_0603_1608Metric_Pad1.08x0.95mm_HandSolder
C16: 47pF; C_0603_1608Metric_Pad1.08x0.95mm_HandSolder
C17, C18: 22uF; C_1206_3216Metric_Pad1.33x1.80mm_HandSolder
L1: 4.7uH; DR74; Part Number DR74-4R7-R
R15: 200k; R_0603_1608Metric_Pad0.98x0.95mm_HandSolder
R16: 10.5k; R_0603_1608Metric_Pad0.98x0.95mm_HandSolder
U2: AN_SY8105; TSOT-23-6_HandSoldering; Part Number AN_SY8105

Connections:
/12V: C16.1, C17.1, C18.1, L1.2, R15.1; also elsewhere on the board
/EN_12V: U2.2 (EN); also elsewhere on the board
/PPHV: C14.1, U2.4 (IN); also elsewhere on the board
GND: C14.2, C17.2, C18.2, R16.2, U2.3 (GND); also elsewhere on the board
unnamed: C15.2, U2.6 (BS)
unnamed: C16.2, R15.2, R16.1, U2.1 (FB)
unnamed: C15.1, L1.1, U2.5 (LX)

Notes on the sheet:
Idsat = 3.6A

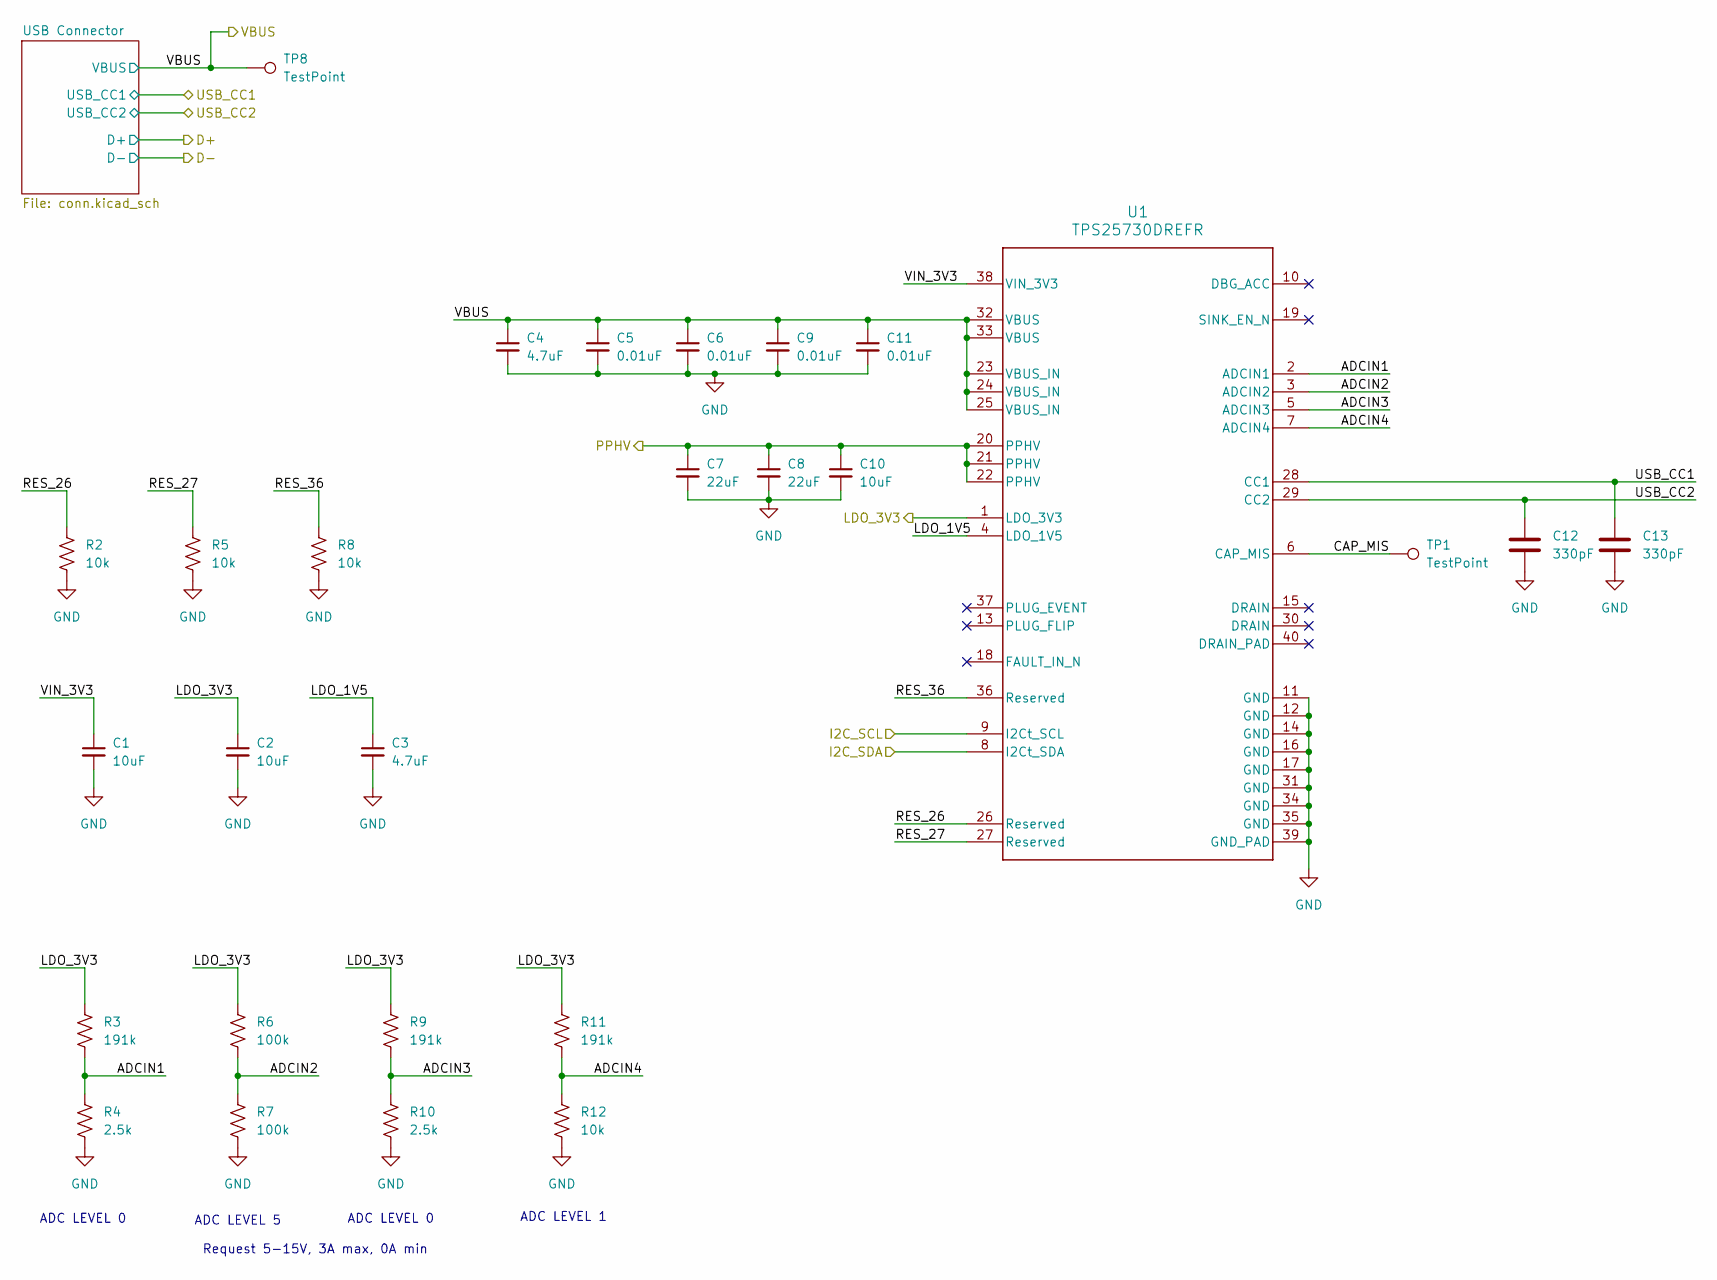
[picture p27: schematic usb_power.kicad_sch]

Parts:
C1, C2, C10: 10uF; C_0603_1608Metric_Pad1.08x0.95mm_HandSolder
C3, C4: 4.7uF; C_0603_1608Metric_Pad1.08x0.95mm_HandSolder
C5, C6, C9, C11: 0.01uF; C_0603_1608Metric_Pad1.08x0.95mm_HandSolder
C7, C8: 22uF; C_1206_3216Metric_Pad1.33x1.80mm_HandSolder
C12, C13: 330pF; C_0603_1608Metric_Pad1.08x0.95mm_HandSolder
R2, R5, R8, R12: 10k; R_0603_1608Metric_Pad0.98x0.95mm_HandSolder
R3, R9, R11: 191k; R_0603_1608Metric_Pad0.98x0.95mm_HandSolder
R4, R10: 2.5k; R_0603_1608Metric_Pad0.98x0.95mm_HandSolder
R6, R7: 100k; R_0603_1608Metric_Pad0.98x0.95mm_HandSolder
TP1, TP8: TestPoint; TestPoint_Pad_1.0x1.0mm
U1: TPS25730DREFR; REF0038A-MFG; Part Number TPS25730DREFR

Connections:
/I2C_SCL: U1.9 (I2Ct_SCL); also elsewhere on the board
/I2C_SDA: U1.8 (I2Ct_SDA); also elsewhere on the board
/PPHV: C7.1, C8.1, C10.1, U1.20 (PPHV), U1.21 (PPHV), U1.22 (PPHV); also elsewhere on the board
/USB Power/ADCIN1: R3.2, R4.1, U1.2 (ADCIN1)
/USB Power/ADCIN2: R6.2, R7.1, U1.3 (ADCIN2)
/USB Power/ADCIN3: R9.2, R10.1, U1.5 (ADCIN3)
/USB Power/ADCIN4: R11.2, R12.1, U1.7 (ADCIN4)
/USB Power/CAP_MIS: TP1.1, U1.6 (CAP_MIS)
/USB Power/LDO_1V5: C3.1, U1.4 (LDO_1V5)
/USB Power/LDO_3V3: C2.1, R3.1, R6.1, R9.1, R11.1, U1.1 (LDO_3V3); also elsewhere on the board
/USB Power/RES_26: R2.1, U1.26 (Reserved)
/USB Power/RES_27: R5.1, U1.27 (Reserved)
/USB Power/RES_36: R8.1, U1.36 (Reserved)
/USB Power/VIN_3V3: C1.1, U1.38 (VIN_3V3)
/USB_CC1: C13.1, U1.28 (CC1); also elsewhere on the board
/USB_CC2: C12.1, U1.29 (CC2); also elsewhere on the board
/VBUS: C4.1, C5.1, C6.1, C9.1, C11.1, TP8.1, U1.23 (VBUS_IN), U1.24 (VBUS_IN), U1.25 (VBUS_IN), U1.32 (VBUS), U1.33 (VBUS); also elsewhere on the board
GND: C1.2, C2.2, C3.2, C4.2, C5.2, C6.2, C7.2, C8.2, C9.2, C10.2, C11.2, C12.2, C13.2, R2.2, R4.2, R5.2, R7.2, R8.2, R10.2, R12.2, U1.11 (GND), U1.12 (GND), U1.14 (GND), U1.16 (GND), U1.17 (GND), U1.31 (GND), U1.34 (GND), U1.35 (GND), U1.39 (GND_PAD); also elsewhere on the board

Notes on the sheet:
Request 5-15V, 3A max, 0A min
ADC LEVEL 5
ADC LEVEL 0
ADC LEVEL 0
ADC LEVEL 1

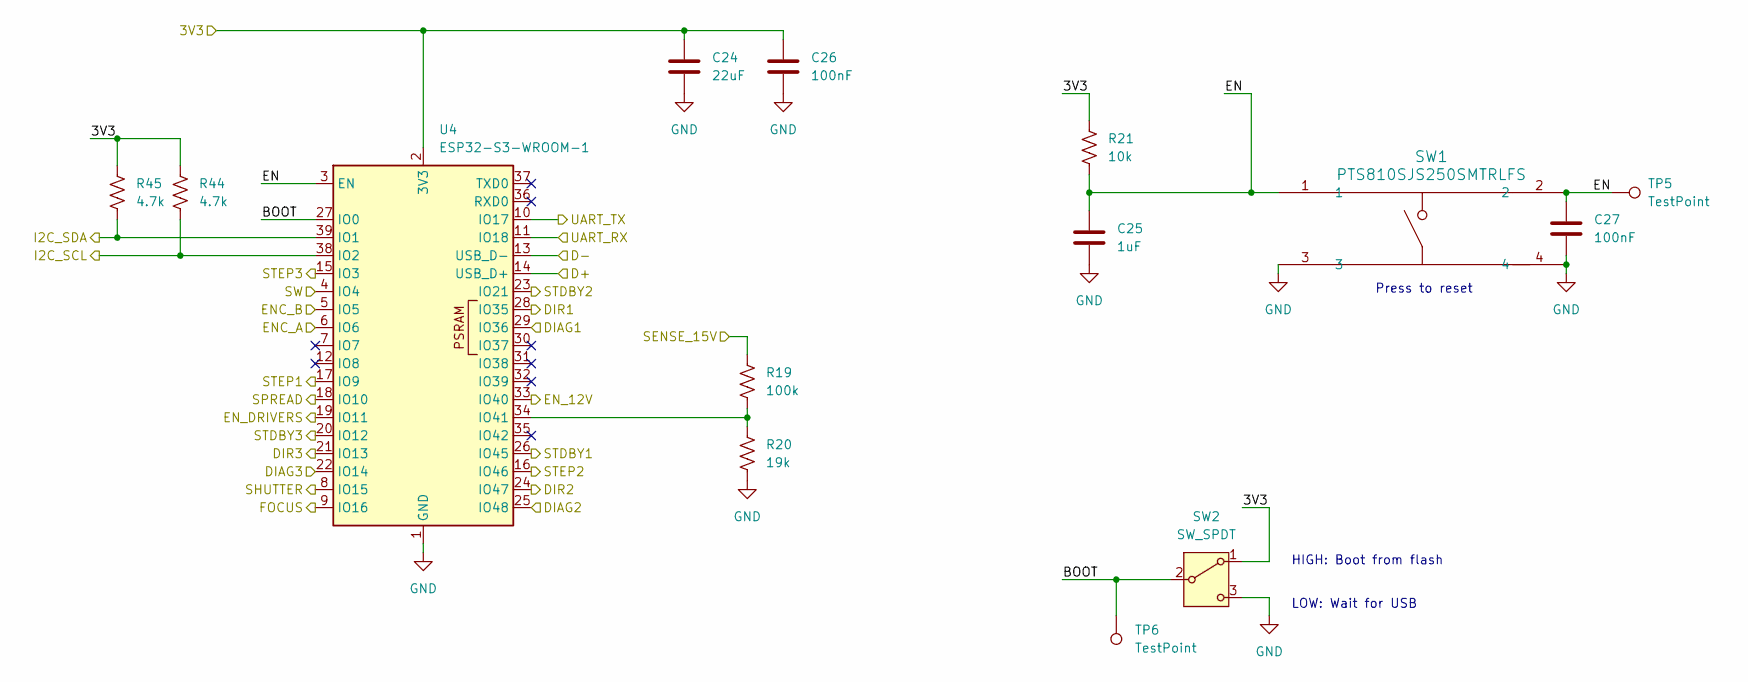
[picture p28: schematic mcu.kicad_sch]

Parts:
C24: 22uF; C_1206_3216Metric_Pad1.33x1.80mm_HandSolder
C25: 1uF; C_0603_1608Metric_Pad1.08x0.95mm_HandSolder
C26, C27: 100nF; C_0603_1608Metric_Pad1.08x0.95mm_HandSolder
R19: 100k; R_0603_1608Metric_Pad0.98x0.95mm_HandSolder
R20: 19k; R_0603_1608Metric_Pad0.98x0.95mm_HandSolder
R21: 10k; R_0603_1608Metric_Pad0.98x0.95mm_HandSolder
R44, R45: 4.7k; R_0603_1608Metric_Pad0.98x0.95mm_HandSolder
SW1: PTS810SJS250SMTRLFS; SMT_MTRLFS_CNK
SW2: SW_SPDT; SS12D07_CNK
TP5, TP6: TestPoint; TestPoint_Pad_1.0x1.0mm
U4: ESP32-S3-WROOM-1; Part Number ESP32-S3-WROOM-1

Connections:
/3V3: C24.1, C26.1, R21.2, R44.2, R45.2, SW2.1 (A), U4.2 (3V3); also elsewhere on the board
/DIAG1: U4.29 (IO36); also elsewhere on the board
/DIAG2: U4.25 (IO48); also elsewhere on the board
/DIAG3: U4.22 (IO14); also elsewhere on the board
/DIR1: U4.28 (IO35); also elsewhere on the board
/DIR2: U4.24 (IO47); also elsewhere on the board
/DIR3: U4.21 (IO13); also elsewhere on the board
/ENC_A: U4.6 (IO6); also elsewhere on the board
/ENC_B: U4.5 (IO5); also elsewhere on the board
/EN_12V: U4.33 (IO40); also elsewhere on the board
/EN_DRIVERS: U4.19 (IO11); also elsewhere on the board
/FOCUS: U4.9 (IO16); also elsewhere on the board
/I2C_SCL: R44.1, U4.38 (IO2); also elsewhere on the board
/I2C_SDA: R45.1, U4.39 (IO1); also elsewhere on the board
/MCU ESP32/BOOT: SW2.2 (B), TP6.1, U4.27 (IO0)
/MCU ESP32/EN: C25.2, C27.1, R21.1, SW1.1, SW1.2, TP5.1, U4.3 (EN)
/MCU ESP32/UART_TX: U4.10 (IO17); also elsewhere on the board
/PPHV: R19.2; also elsewhere on the board
/SHUTTER: U4.8 (IO15); also elsewhere on the board
/SPREAD: U4.18 (IO10); also elsewhere on the board
/STDBY1: U4.26 (IO45); also elsewhere on the board
/STDBY2: U4.23 (IO21); also elsewhere on the board
/STDBY3: U4.20 (IO12); also elsewhere on the board
/STEP1: U4.17 (IO9); also elsewhere on the board
/STEP2: U4.16 (IO46); also elsewhere on the board
/STEP3: U4.15 (IO3); also elsewhere on the board
/SW: U4.4 (IO4); also elsewhere on the board
/UART_TX/RX: U4.11 (IO18); also elsewhere on the board
/USB_D+: U4.14 (USB_D+); also elsewhere on the board
/USB_D-: U4.13 (USB_D-); also elsewhere on the board
GND: C24.2, C25.1, C26.2, C27.2, R20.1, SW1.3, SW1.4, SW2.3 (C), U4.1 (GND), U4.40 (GND), U4.41 (GND); also elsewhere on the board
unnamed: R19.1, R20.2, U4.34 (IO41)

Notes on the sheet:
Press to reset
HIGH: Boot from flash LOW: Wait for USB

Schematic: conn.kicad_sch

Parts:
D1, D2, D3, D4: ESD441; D_0402_1005Metric_Pad0.77x0.64mm_HandSolder
D5: T4F10A; Nexperia_CFP3_SOD-123W
J5: USB_C_Receptacle_USB2.0_16P; CONN_8p94X6p5X3p16_12L_GCC
R36, R37: 5.1k+-10%; R_0603_1608Metric_Pad0.98x0.95mm_HandSolder

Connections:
/USB_CC1: D3.1 (K), J5.A5 (CC1), R36.1; also elsewhere on the board
/USB_CC2: D4.1 (K), J5.B5 (CC2), R37.1; also elsewhere on the board
/USB_D+: D1.1 (K), J5.A6 (D+), J5.B6 (D+); also elsewhere on the board
/USB_D-: D2.1 (K), J5.A7 (D-), J5.B7 (D-); also elsewhere on the board
/VBUS: D5.1 (K), J5.A4 (VBUS), J5.A9 (VBUS), J5.B4 (VBUS), J5.B9 (VBUS); also elsewhere on the board
GND: D1.2 (A), D2.2 (A), D3.2 (A), D4.2 (A), D5.2 (A), J5.A1 (GND), J5.A12 (GND), J5.B1 (GND), J5.B12 (GND), J5.S1 (SHIELD), R36.2, R37.2; also elsewhere on the board

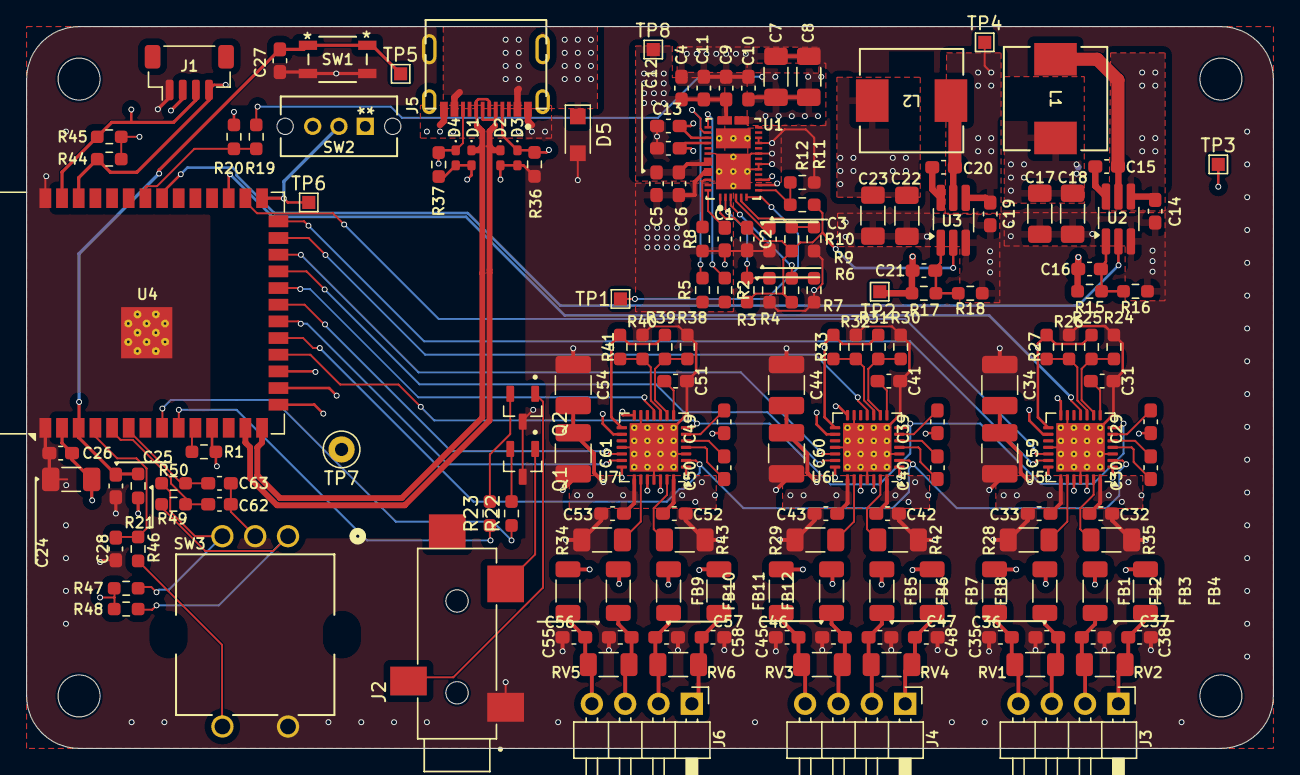
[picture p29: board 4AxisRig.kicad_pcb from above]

Board: 4 copper layers, 95.0 x 55.0 mm, 166 parts (0 on the bottom side), 108 nets.

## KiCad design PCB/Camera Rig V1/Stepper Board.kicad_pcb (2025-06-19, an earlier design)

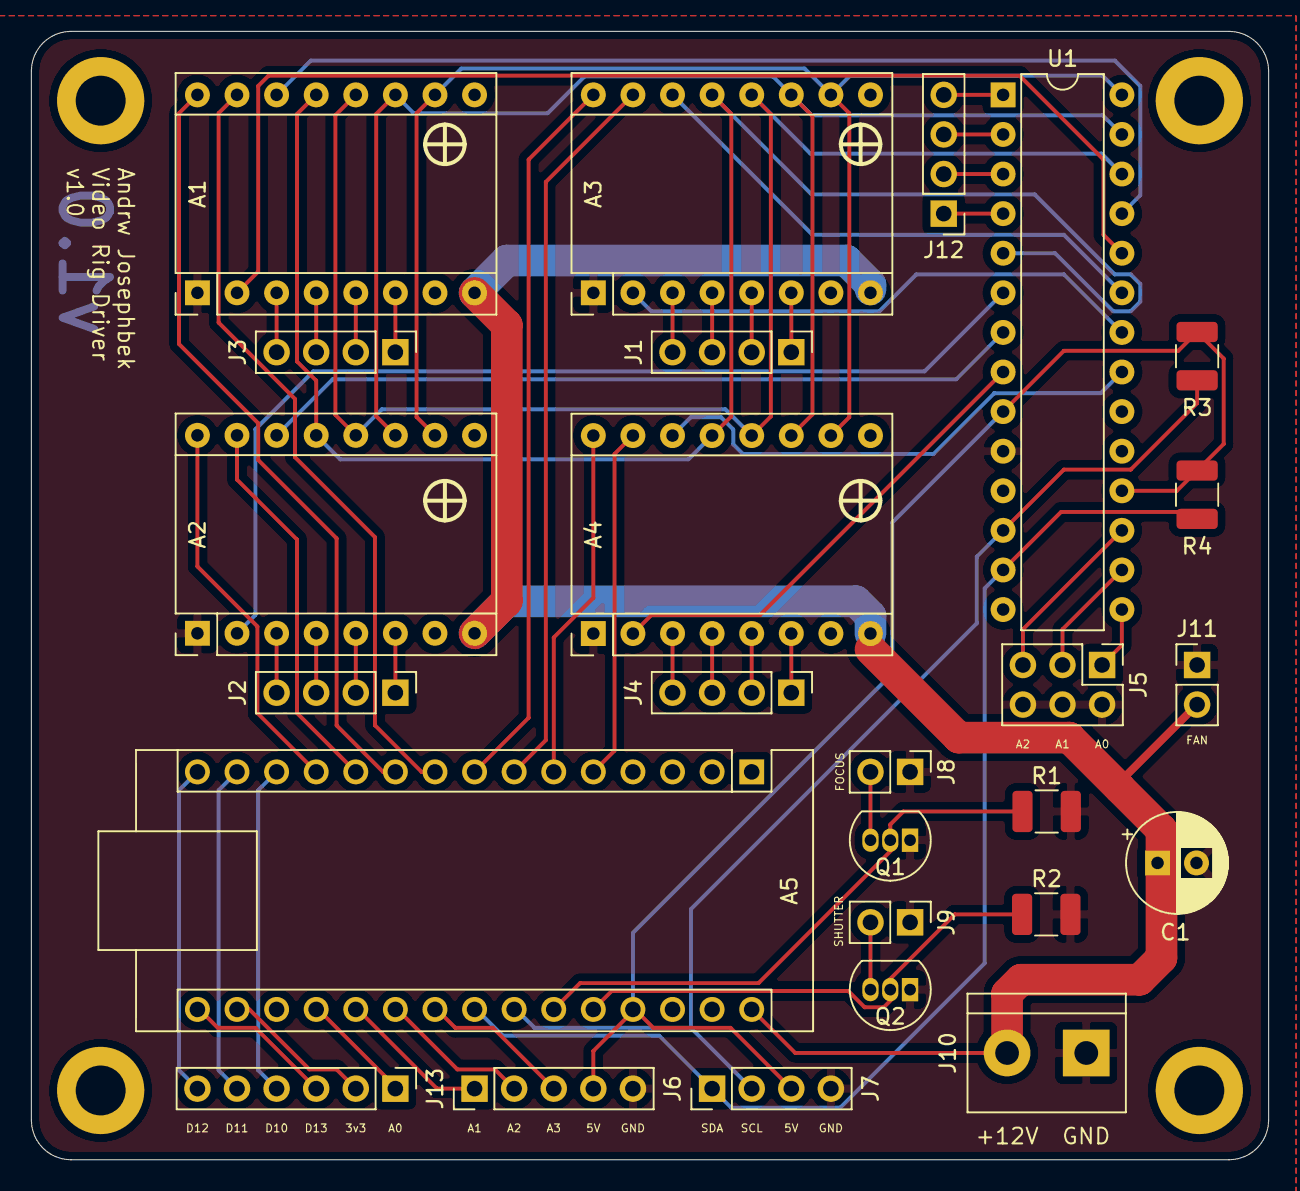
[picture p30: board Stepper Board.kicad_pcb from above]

Board: 2 copper layers, 79.4 x 72.4 mm, 30 parts (0 on the bottom side), 61 nets.

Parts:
 : MountingHole_3.2mm_M3_DIN965_Pad
 #2,  #3,  #4: MountingHole_3.2mm_M3_DIN965_Pad
A1, A2, A3, A4: Pololu_Breakout_DRV8825; Pololu_Breakout-16_15.2x20.3mm
A5: Arduino_Nano_v3.x; Arduino_Nano
C1: 220uF; CP_Radial_D6.3mm_P2.50mm
J1, J2, J3, J4: Stepper Header; PinHeader_1x04_P2.54mm_Vertical
J5: Address Header; PinHeader_2x03_P2.54mm_Vertical
J6: R.Encoder Header; PinHeader_1x05_P2.54mm_Vertical
J7: LCD Header; PinHeader_1x04_P2.54mm_Vertical
J8: Focus; PinHeader_1x02_P2.54mm_Vertical
J9: Shot; PinHeader_1x02_P2.54mm_Vertical
J10: Power (+12V); TerminalBlock_bornier-2_P5.08mm
J11: Fan Header; PinHeader_1x02_P2.54mm_Vertical
J12: Extra Header I2C; PinHeader_1x04_P2.54mm_Vertical
J13: Extra Header Direct; PinHeader_1x06_P2.54mm_Vertical
Q1, Q2: 2N7000; TO-92_Inline
R3, R4, R7, R8: SM 10K; R_1210_3225Metric_Pad1.30x2.65mm_HandSolder
U1: MCP23017_SP; DIP-28_W7.62mm

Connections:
+3V3: A5.17, J13.2
+5V: A5.27, J6.4, J7.3, R3.1, R4.1, U1.9, U1.18
A0: A5.19, J13.1
A1: A5.20, J6.1
A1(1): A1.4, J1.3
A1(2): A2.4, J2.3
A1(3): A3.4, J3.3
A1(4): A4.4, J4.3
A2: A5.21, J6.2
A2(1): A1.3, J1.4
A2(2): A2.3, J2.4
A2(3): A3.3, J3.4
A2(4): A4.3, J4.4
A3: A5.22, J6.3
A6: A5.25, Q1.2
A7: A5.26, Q2.2
B1(1): A1.5, J1.2
B1(2): A2.5, J2.2
B1(3): A3.5, J3.2
B1(4): A4.5, J4.2
B2(1): A1.6, J1.1
B2(2): A2.6, J2.1
B2(3): A3.6, J3.1
B2(4): A4.6, J4.1
D13: A5.16, J13.3
DIR1: A1.16, A5.8
DIR2: A2.16, A5.12
DIR3: A3.16, A5.10
DIR4: A4.16, A5.6
FLT1: A1.2, U1.22
FLT2: A2.2, U1.6
FLT3: A3.2, U1.24
FLT4: A4.2, U1.8
GND: A1.1, A2.1, A3.1, A4.1, A5.29, C1.2, J5.2, J5.4, J5.6, J6.5, J7.4, J8.1, J9.1, J10.1, J11.1, Q1.1, Q2.1, R7.1, R8.1, U1.10
M0: A1.10, A2.10, A3.10, A4.10, U1.28
M1: A1.11, A2.11, A3.11, A4.11, U1.27
M2: A1.12, A2.12, A3.12, A4.12, U1.26
unnamed: A5.13, J13.4
unnamed: A5.14, J13.5
unnamed: A5.15, J13.6
unnamed: J5.1, U1.15
unnamed: J5.3, U1.16
unnamed: J5.5, U1.17
unnamed: J8.2, Q1.3
unnamed: J9.2, Q2.3
unnamed: J12.1, U1.4
unnamed: J12.2, U1.3
unnamed: J12.3, U1.2
unnamed: J12.4, U1.1
RST: A1.13, A2.13, A3.13, A4.13, U1.5
SCK: A5.24, J7.2, R4.2, U1.12
SDA: A5.23, J7.1, R3.2, U1.13
SLEEP1: A1.14, U1.23
SLEEP2: A2.14, U1.7
SLEEP3: A3.14, U1.25
SLEEP4: A4.14, U1.21
STEP1: A1.15, A5.7
STEP2: A2.15, A5.11
STEP3: A3.15, A5.9
STEP4: A4.15, A5.5
VCC: A1.8, A2.8, A3.8, A4.8, A5.30, C1.1, J10.2, J11.2

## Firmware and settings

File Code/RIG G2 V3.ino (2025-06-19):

#include <LiquidCrystal_I2C.h>

#include <Adafruit_MCP23017.h>

//Definitions
#define STEP4 2
#define DIR4 3
#define STEP1 4
#define DIR1 5
#define STEP3 6
#define DIR3 7
#define STEP2 8
#define DIR2 9

#define SDA 4
#define SCL 5

#define M0 7
#define M1 6
#define M2 5

#define RESET 12
#define SLEEP1 2
#define SLEEP2 14
#define SLEEP3 4
#define SLEEP4 0

#define FAULT1 1
#define FAULT2 13
#define FAULT3 3
#define FAULT4 15
#define FOCUS A6
#define SHOT A7

#define inputCLK A2
#define inputDT A1
#define encSwitch A3

#define cursorPulseThreshold 50
#define valuePulseThreshold 50

#define screenElements 5
#define screenElementsSettings 7
#define SPEED 500

//

LiquidCrystal_I2C lcd(0x27, 20, 4);
Adafruit_MCP23017 mcp;

//Motion Variables
float exposure;
float pause;
long shots;

float Motor1Steps;
float Motor2Steps;
float Motor3Steps;
float Motor4Steps;

bool sleep;
float incSpeed = 0;

int Motor1Jog;
int Motor2Jog;
int Motor3Jog;
int Motor4Jog;
int MicroStep;

//

//Display Variables
int currentStateCLK;
int previousStateCLK;

int timeSinceUpdate;
bool screenHasUpdated = false;
int timeWaited;
bool EditView = false;
int ViewCounter;
int ViewSelector;

bool prevButtonState = true;
bool currButtonState = true;
int MenuSelector = 0;
int fractionSelector;

int totalSteps;

byte degrees[] = {
  B11100,
  B10100,
  B11100,
  B00000,
  B00000,
  B00000,
  B00000,
  B00000
};

byte stairs[] = {
  B00001,
  B00011,
  B00101,
  B01001,
  B10001,
  B10001,
  B11111,
  B00000
};

byte reverseStairs[] = {
  B10000,
  B11000,
  B10100,
  B10010,
  B10001,
  B10001,
  B11111,
  B00000
};
//

byte incSymb[] = {
  B01000,
  B00100,
  B10010,
  B01001,
  B10010,
  B00100,
  B01000,
  B00000
};

byte moon[] = {
  B00000,
  B00110,
  B01100,
  B11000,
  B11000,
  B11001,
  B01111,
  B00110
};
void setup() {
  mcp.begin();
  //pinmodes
  pinMode(STEP4, OUTPUT);
  pinMode(DIR4, OUTPUT);
  pinMode(STEP1, OUTPUT);
  pinMode(DIR1, OUTPUT);
  pinMode(STEP3, OUTPUT);
  pinMode(DIR3, OUTPUT);
  pinMode(STEP2, OUTPUT);
  pinMode(DIR2, OUTPUT);
  pinMode(FOCUS, OUTPUT);
  pinMode(SHOT, OUTPUT);

  pinMode(inputCLK, INPUT);
  pinMode(inputDT, INPUT);
  pinMode(12, OUTPUT);

  mcp.pinMode(M0, OUTPUT);
  mcp.pinMode(M1, OUTPUT);
  mcp.pinMode(M2, OUTPUT);

  mcp.pinMode(RESET, OUTPUT);

  mcp.pinMode(SLEEP1, OUTPUT);
  mcp.pinMode(SLEEP2, OUTPUT);
  mcp.pinMode(SLEEP3, OUTPUT);
  mcp.pinMode(SLEEP4, OUTPUT);

  mcp.pinMode(FAULT1, INPUT);
  mcp.pinMode(FAULT2, INPUT);
  mcp.pinMode(FAULT3, INPUT);
  mcp.pinMode(FAULT4, INPUT);

  //Enabling drivers
  mcp.digitalWrite(RESET, HIGH);

  //Micro-step mode  
  mcp.digitalWrite(M0, LOW);
  mcp.digitalWrite(M1, LOW);
  mcp.digitalWrite(M2, LOW);

  mcp.digitalWrite(SLEEP1, LOW);
  mcp.digitalWrite(SLEEP2, LOW);
  mcp.digitalWrite(SLEEP3, LOW);
  mcp.digitalWrite(SLEEP4, LOW);
  //

  previousStateCLK = digitalRead(inputCLK);
  lcd.init();
  lcd.backlight();
  lcd.createChar(0, degrees);
  lcd.createChar(1, stairs);
  lcd.createChar(2, reverseStairs);
  lcd.createChar(3, incSymb);
  lcd.createChar(4, moon);




  //GUI
  mainMenu();

}

void loop() {

  prevButtonState = currButtonState;
  currButtonState = digitalRead(encSwitch);

  if (prevButtonState == false && currButtonState == true) {
    EditView = !EditView;
  }

  //Main Menu
  if (MenuSelector == 0) {
    //Select Value to Edit
    if (EditView == false) {

      ViewCounter = ViewCounter + rotaryEncoder(1);
      if (ViewCounter < 0) {
        ViewCounter = 10;
      }
      if (ViewCounter > 10) {
        ViewCounter = 0;
      }
      ViewSelector = ViewCounter / 2;

      lcd.cursor_on();
      if (ViewSelector == 0) {
        encoderLCDCursor(0, 0);
      }
      if (ViewSelector == 1) {
        encoderLCDCursor(3, 0);
      }
      if (ViewSelector == 2) {
        encoderLCDCursor(3, 1);
      }
      if (ViewSelector == 3) {
        encoderLCDCursor(3, 2);
      }
      if (ViewSelector == 4) {
        encoderLCDCursor(19, 0);
      }
      if (ViewSelector == 5) {
        encoderLCDCursor(19, 3);
      }
    }

    //Edit values when in Edit Mode
    if (EditView == true) {

      //String message, int x, int y, int wipe
      if (ViewSelector == 0) {
        MenuSelector = 2;
        EditView = false;
        motorMenu();
      }
      if (ViewSelector == 1) {
        shots = rotaryEncoder(5) + shots;
        encoderLCDPrint(String(shots), 3, 0, 6);
      }
      if (ViewSelector == 2) {
        pause = float(rotaryEncoder(1)) / 8 + pause;
        encoderLCDPrint(String(pause), 3, 1, 6);
      }
      if (ViewSelector == 3) {
        exposure = float(rotaryEncoder(1)) / 8 + exposure;
        encoderLCDPrint(String(exposure), 3, 2, 6);
      }
      if (ViewSelector == 4 && prevButtonState == false && currButtonState == true) {
        MenuSelector = 1;
        EditView = false;
        lcd.clear();
        settings();
        ViewCounter = 0;

      }
      if (ViewSelector == 5 && prevButtonState == false && currButtonState == true) {
        TimeLapse();
      }
    }
  }
  //

  //Settings
  if (MenuSelector == 1) {

    if (EditView == false) {

      if (Motor1Jog != 0) {
        stepMotor(((1 << fractionSelector) * (100L * Motor1Jog)) / 3, 2500 - (490 * fractionSelector), STEP1, DIR1, SLEEP1);
        Motor1Jog = 0;
        lcd.setCursor(4, 0);
        lcd.print("0   ");
        lcd.setCursor(4, 0);
      }

      if (Motor2Jog != 0) {
        stepMotor(((1 << fractionSelector) * (100L * Motor2Jog)) / 3, 2500 - (490 * fractionSelector), STEP2, DIR2, SLEEP2);
        Motor2Jog = 0;
        lcd.setCursor(4, 1);
        lcd.print("0   ");
        lcd.setCursor(4, 1);
      }
      if (Motor3Jog != 0) {
        stepMotor((1 << fractionSelector) * ((100L * Motor3Jog) / 3), 2500 - (490 * fractionSelector), STEP3, DIR3, SLEEP3);
        Motor3Jog = 0;
        lcd.setCursor(4, 2);
        lcd.print("0   ");
        lcd.setCursor(4, 2);
      }
      if (Motor4Jog != 0) {
        stepMotor((1 << fractionSelector) * ((100L * Motor4Jog) / 3), 2500 - (490 * fractionSelector), STEP4, DIR4, SLEEP4);
        Motor4Jog = 0;
        lcd.setCursor(4, 3);
        lcd.print("0   ");
        lcd.setCursor(4, 3);
      }

      mcp.digitalWrite(SLEEP1, LOW);
      mcp.digitalWrite(SLEEP2, LOW);
      mcp.digitalWrite(SLEEP3, LOW);
      mcp.digitalWrite(SLEEP4, LOW);

      ViewCounter = ViewCounter + rotaryEncoder(1);

      if (ViewCounter < 0) {
        ViewCounter = 17;
      }
      if (ViewCounter > 17) {
        ViewCounter = 0;
      }
      ViewSelector = ViewCounter / 2;

      lcd.cursor_on();

      if (ViewSelector == 0) {
        encoderLCDCursor(0, 0);
      }

      if (ViewSelector == 1) {
        encoderLCDCursor(4, 0);
      }
      if (ViewSelector == 2) {
        encoderLCDCursor(4, 1);
      }
      if (ViewSelector == 3) {
        encoderLCDCursor(4, 2);
      }
      if (ViewSelector == 4) {
        encoderLCDCursor(4, 3);
      }
      if (ViewSelector == 5) {
        encoderLCDCursor(9, 0);
      }
      if (ViewSelector == 6) {
        encoderLCDCursor(9, 1);
      }
      if (ViewSelector == 7) {
        encoderLCDCursor(9, 2);
      }
      if (ViewSelector == 8) {
        encoderLCDCursor(8, 3);
      }

    }

    //Edit values when in Edit Mode
    if (EditView == true) {
      if (ViewSelector == 1) {
        Motor1Jog = rotaryEncoder(5) + Motor1Jog;
        encoderLCDPrint(String(Motor1Jog), 4, 0, 4);
      }

      if (ViewSelector == 2) {
        Motor2Jog = rotaryEncoder(5) + Motor2Jog;

        encoderLCDPrint(String(Motor2Jog), 4, 1, 4);
      }

      if (ViewSelector == 3) {
        Motor3Jog = rotaryEncoder(5) + Motor3Jog;

        encoderLCDPrint(String(Motor3Jog), 4, 2, 4);
      }

      if (ViewSelector == 4) {
        Motor4Jog = rotaryEncoder(5) + Motor4Jog;
        encoderLCDPrint(String(Motor4Jog), 4, 3, 4);
      }

      if (ViewSelector == 5) {
        MicroStep = rotaryEncoder(1) + MicroStep;
        fractionSelector = (MicroStep) / 2 % 6;

        if (screenHasUpdated == false) {
          if ((1 << fractionSelector) == 1) {
            mcp.digitalWrite(M0, LOW);
            mcp.digitalWrite(M1, LOW);
            mcp.digitalWrite(M2, LOW);
          }
          if ((1 << fractionSelector) == 2) {
            mcp.digitalWrite(M0, HIGH);
            mcp.digitalWrite(M1, LOW);
            mcp.digitalWrite(M2, LOW);
          }
          if ((1 << fractionSelector) == 4) {
            mcp.digitalWrite(M0, LOW);
            mcp.digitalWrite(M1, HIGH);
            mcp.digitalWrite(M2, LOW);
          }
          if ((1 << fractionSelector) == 8) {
            mcp.digitalWrite(M0, HIGH);
            mcp.digitalWrite(M1, HIGH);
            mcp.digitalWrite(M2, LOW);
          }
          if ((1 << fractionSelector) == 16) {
            mcp.digitalWrite(M0, LOW);
            mcp.digitalWrite(M1, LOW);
            mcp.digitalWrite(M2, HIGH);
          }
          if ((1 << fractionSelector) == 32) {
            mcp.digitalWrite(M0, HIGH);
            mcp.digitalWrite(M1, HIGH);
            mcp.digitalWrite(M2, HIGH);
          }
        }
        encoderLCDPrint("1/" + String(1 << fractionSelector), 9, 0, 4);

      }
      if (ViewSelector == 6 && prevButtonState == false && currButtonState == true) {
        sleep = !sleep;
        if (sleep) {
          lcd.setCursor(9, 1);
          lcd.print("true ");
          lcd.setCursor(9, 1);
        } else {
          lcd.setCursor(9, 1);
          lcd.print("false");
          lcd.setCursor(9, 1);
        }
        EditView = false;
      }
      
      if (ViewSelector == 7) {
        incSpeed = float(rotaryEncoder(1))/4 + incSpeed;
        encoderLCDPrint(String(incSpeed), 9, 2, 6);
      }

      if (ViewSelector == 8 && prevButtonState == false && currButtonState == true) {
        mcp.digitalWrite(RESET, LOW);
        delay(250);
        mcp.digitalWrite(RESET, HIGH);
        EditView = false;
      }


      if (ViewSelector == 0 && prevButtonState == false && currButtonState == true) {
        EditView = false;
        MenuSelector = 0;
        lcd.clear();
        mainMenu();
        ViewCounter = 0;
      }
    }
  }
  //

  //Motor Menu
  if (MenuSelector == 2) {

    if (EditView == false) {

      ViewCounter = ViewCounter + rotaryEncoder(1);
      if (ViewCounter < 0) {
        ViewCounter = 8;
      }
      if (ViewCounter > 8) {
        ViewCounter = 0;
      }
      ViewSelector = ViewCounter / 2;

      if (ViewSelector == 0) {
        encoderLCDCursor(3, 0);
      }
      if (ViewSelector == 1) {
        encoderLCDCursor(3, 1);
      }
      if (ViewSelector == 2) {
        encoderLCDCursor(3, 2);
      }
      if (ViewSelector == 3) {
        encoderLCDCursor(3, 3);
      }
      if (ViewSelector == 4) {
        encoderLCDCursor(19, 0);
      }
    }
    if (EditView == true) {
      if (ViewSelector == 0) {
        Motor1Steps = float(rotaryEncoder(1)) / (1 << fractionSelector) + Motor1Steps;
        encoderLCDPrint(String(Motor1Steps), 3, 0, 6);
      }
      if (ViewSelector == 1) {
        Motor2Steps = float(rotaryEncoder(1)) / (1 << fractionSelector) + Motor2Steps;
        encoderLCDPrint(String(Motor2Steps), 3, 1, 6);
      }
      if (ViewSelector == 2) {
        Motor3Steps = float(rotaryEncoder(1)) / (1 << fractionSelector) + Motor3Steps;
        encoderLCDPrint(String(Motor3Steps), 3, 2, 6);
      }
      if (ViewSelector == 3) {
        Motor4Steps = float(rotaryEncoder(1)) / (1 << fractionSelector) + Motor4Steps;
        encoderLCDPrint(String(Motor4Steps), 3, 3, 6);
      }
      if (ViewSelector == 4) {
        mainMenu();
        MenuSelector = 0;
        EditView = false;
        ViewCounter = 0;
      }
    }
  }
  //

}


// timelapse ---------------------
void TimeLapse() {
  lcd.noCursor();
  MenuSelector = 3;
  lcd.clear();
  mcp.digitalWrite(RESET, LOW);
  mcp.digitalWrite(RESET, HIGH);
  int shotsRemaining = shots;

  fractionSelector = (MicroStep) / 2 % 6;

  if (incSpeed == 0) {
    incSpeed = (2500 - (490 * fractionSelector))/1000;
  }

  totalSteps = Motor1Steps + Motor2Steps + Motor3Steps + Motor4Steps;

  //Setting motor direction
  if (Motor1Steps < 0) {
    digitalWrite(DIR1, HIGH);
  }
  if (Motor2Steps < 0) {
    digitalWrite(DIR2, HIGH);
  }
  if (Motor3Steps < 0) {
    digitalWrite(DIR3, HIGH);
  }
  if (Motor4Steps < 0) {
    digitalWrite(DIR4, HIGH);
  }

  delay(1000);

  //making sure 
  mcp.digitalWrite(RESET, HIGH);
  mcp.digitalWrite(SLEEP1, HIGH);
  mcp.digitalWrite(SLEEP2, HIGH);
  mcp.digitalWrite(SLEEP3, HIGH);
  mcp.digitalWrite(SLEEP4, HIGH);


  lcd.setCursor(0, 2);
 lcd.print("Debug Info:");


  lcd.setCursor(0, 3);
  lcd.print(round(Motor1Steps));
  lcd.print(" ");
  lcd.print(round(Motor2Steps));
  lcd.print(" ");
  lcd.print(round(Motor3Steps));
  lcd.print(" ");
  lcd.print(round(Motor4Steps));
  lcd.print(" ");

delay(3000);  

lcd.clear();

  for (shotsRemaining; shotsRemaining > 0; shotsRemaining--) {
    


    //Override
    if (digitalRead(encSwitch) == LOW) {
      lcd.clear();
      delay(1500);
      break;
    }



    //Updating completion value
    float percentFinished = 1 - (float(shotsRemaining) / float(shots));
    lcd.setCursor(4, 1);
    lcd.print("                    ");
    lcd.setCursor(10 - String(String(percentFinished * 100) + "% complete").length() / 2, 1);
    lcd.print(String(percentFinished * 100) + "% complete");
    lcd.setCursor(0, 3);

    //Updating time remaining value
    int timeLeft = ((exposure + pause) * shotsRemaining + (totalSteps / 500) * shotsRemaining) / 60;
    lcd.setCursor(0, 2);
    lcd.print("                    ");
    lcd.setCursor(10 - String("T=" + String(timeLeft) + "min").length() / 2, 2);
    lcd.print(String("T=" + String(timeLeft) + "min"));
    delay((pause * 1000));

    //Debug
  /*  lcd.setCursor(0, 3);
    lcd.print("      ");
    lcd.setCursor(0, 3);
    lcd.print(incSpeed);
    lcd.print("ms");
    */
    //Taking the picture
    digitalWrite(12, HIGH);
    delay((exposure * 1000));
    digitalWrite(12, LOW);

    //Waking the motors
    if (sleep) {
      mcp.digitalWrite(SLEEP1, HIGH);
      mcp.digitalWrite(SLEEP2, HIGH);
      mcp.digitalWrite(SLEEP3, HIGH);
      mcp.digitalWrite(SLEEP4, HIGH);
    }

    delay(500);

    if (Motor1Steps != 0) {
      for (int u = Motor1Steps * (1 << fractionSelector); u > 0; u--) {
        digitalWrite(STEP1, HIGH);
        delay(incSpeed);
        digitalWrite(STEP1, LOW);
      }
    }

    if (Motor2Steps != 0) {
      for (int u = Motor2Steps * (1 << fractionSelector); u > 0; u--) {
        digitalWrite(STEP2, HIGH);
        delay(incSpeed);
        digitalWrite(STEP2, LOW);
      }
    }

    if (Motor3Steps != 0) {
      for (int u = Motor3Steps * (1 << fractionSelector); u > 0; u--) {
        digitalWrite(STEP3, HIGH);
        delay(incSpeed);
        digitalWrite(STEP3, LOW);
      }
    }

    if (Motor4Steps != 0) {
      for (int u = Motor4Steps * (1 << fractionSelector); u > 0; u--) {
        digitalWrite(STEP3, HIGH);
        delay(incSpeed);
        digitalWrite(STEP3, LOW);
      }
    }

    if (sleep) {
      mcp.digitalWrite(SLEEP1, LOW);
      mcp.digitalWrite(SLEEP2, LOW);
      mcp.digitalWrite(SLEEP3, LOW);
      mcp.digitalWrite(SLEEP4, LOW);
    }
  }

  lcd.clear();
  EditView = false;
  mainMenu();
  MenuSelector = 0;
  ViewCounter = 0;
  lcd.setCursor(0, 0);

}

int rotaryEncoder(int increment) {

  int counter = 0;
  counter = 0;

  currentStateCLK = digitalRead(inputCLK);

  if (currentStateCLK != previousStateCLK) {
    timeSinceUpdate = millis();

    if (digitalRead(inputDT) != currentStateCLK) {
      counter = counter - increment;
      screenHasUpdated = false;
    } else {
      counter = counter + increment;
      screenHasUpdated = false;
    }

  }
  previousStateCLK = currentStateCLK;

  timeWaited = millis() - timeSinceUpdate;

  return counter;

}

void encoderLCDPrint(String message, int x, int y, int wipe) {
  if (timeWaited > valuePulseThreshold && screenHasUpdated == false) {

    for (int spaces = 0; spaces < wipe; spaces++) {
      lcd.print(" ");
    }
    lcd.setCursor(x, y);
    lcd.print(message);

    if (MenuSelector == 0) {
      if (ViewSelector == 1 or ViewSelector == 2 or ViewSelector == 3) {
        lcd.setCursor(0, 3);
        lcd.print("          ");

        float duration = ((exposure + pause) * shots + (totalSteps / 500)) / 60;
        lcd.setCursor(1, 3);

        if (duration < 60) {
          lcd.print(duration);
          lcd.print("min");
        } else {
          lcd.print(duration / 60);
          lcd.print("hr");
        }
      }
    }

    if (MenuSelector == 2) {
      if (ViewSelector == 0 or ViewSelector == 1 or ViewSelector == 2) {
        lcd.setCursor(11, y);
        lcd.print("      ");

        lcd.setCursor(11, y);
        lcd.print(shots * (message.toFloat() * 3) / 100);
        lcd.write(0);

      }
    }
    lcd.setCursor(x, y);
    screenHasUpdated = true;
  }
}


void encoderLCDCursor(int x, int y) {
  if (timeWaited > cursorPulseThreshold && screenHasUpdated == false) {
    lcd.setCursor(x, y);
    screenHasUpdated = true;
  }
}

void settings() {
  lcd.setCursor(1, 0);
  lcd.write(2);
  lcd.print("1 ");
  lcd.setCursor(1, 1);
  lcd.write(2);
  lcd.print("2 ");
  lcd.setCursor(1, 2);
  lcd.write(2);
  lcd.print("3 ");
  lcd.setCursor(1, 3);
  lcd.write(2);
  lcd.print("4 ");

  lcd.setCursor(8, 0);
  lcd.write(1);
  lcd.setCursor(8, 3);
  lcd.print("Reset");
  lcd.setCursor(8, 2);
  lcd.write(3);
  lcd.print(incSpeed);
  lcd.setCursor(8, 1);
  lcd.write(4);
  if (sleep) {
    lcd.setCursor(9, 1);
    lcd.print("true ");
    lcd.setCursor(9, 1);
  } else {
    lcd.setCursor(9, 1);
    lcd.print("false");
    lcd.setCursor(9, 1);
  }

  lcd.setCursor(4, 0);
  lcd.print(Motor1Jog);
  lcd.setCursor(4, 1);
  lcd.print(Motor2Jog);
  lcd.setCursor(4, 2);
  lcd.print(Motor3Jog);
  lcd.setCursor(4, 3);
  lcd.print(Motor4Jog);
  lcd.setCursor(9, 0);
  lcd.print("1/" + String(1 << fractionSelector));
  lcd.setCursor(0, 0);
  lcd.print("<");

  lcd.setCursor(0, 0);

}

void mainMenu() {
  lcd.clear();
  lcd.setCursor(0, 0);
  lcd.print("<");

  lcd.setCursor(1, 0);
  lcd.print("S:");
  lcd.setCursor(1, 1);
  lcd.print("D:");
  lcd.setCursor(1, 2);
  lcd.print("E:");

  lcd.setCursor(3, 0);
  lcd.print(shots);
  lcd.setCursor(3, 1);
  lcd.print(pause);
  lcd.setCursor(3, 2);
  lcd.print(exposure);
  lcd.setCursor(1, 3);
  lcd.print(((exposure + pause) * shots + (totalSteps / 500)) / 60);
  lcd.print("min");

  lcd.setCursor(19, 0);
  lcd.print(">");
  lcd.setCursor(19, 3);
  lcd.print("*");
  lcd.cursor();

}

void motorMenu() {
  lcd.clear();

  lcd.setCursor(19, 0);
  lcd.print(">");

  lcd.setCursor(0, 0);
  lcd.write(1);
  lcd.print("1 ");
  lcd.print(Motor1Steps);
  lcd.setCursor(0, 1);
  lcd.write(1);
  lcd.print("2 ");
  lcd.print(Motor2Steps);
  lcd.setCursor(0, 2);
  lcd.write(1);
  lcd.print("3 ");
  lcd.print(Motor3Steps);
  lcd.setCursor(0, 3);
  lcd.write(1);
  lcd.print("4 ");
  lcd.print(Motor4Steps);

  lcd.setCursor(11, 0);
  lcd.print(shots * (Motor1Steps * 3) / 100);
  lcd.write(0);

  lcd.setCursor(11, 1);
  lcd.print(shots * (Motor2Steps * 3) / 100);
  lcd.write(0);

  lcd.setCursor(11, 2);
  lcd.print(shots * (Motor3Steps * 3) / 100);
  lcd.write(0);

  lcd.setCursor(11, 3);
  lcd.print(shots * (Motor4Steps * 3) / 100);
  lcd.write(0);

  lcd.setCursor(3, 0);

  ViewCounter = 0;

  lcd.cursor();

}

void stepMotor(long jogSteps, int speed, int stepPin, int dirPin, int sleep) {

  mcp.digitalWrite(RESET, HIGH);
  mcp.digitalWrite(sleep, HIGH);

  long steps = abs(jogSteps);

  if (jogSteps > 0) {
    digitalWrite(dirPin, HIGH);
  } else {
    digitalWrite(dirPin, LOW);
  }

  for (steps; steps > 0; steps--) {
    digitalWrite(stepPin, HIGH);
    delayMicroseconds(speed);
    digitalWrite(stepPin, LOW);
  }
  mcp.digitalWrite(sleep, LOW);

}

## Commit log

2025-06-19 Initial Commit
    Moved files from local machine to GitHub
    [Stepper Board.kicad_pcb]
2025-06-19 Added 3D Files
    [Cradle v13.f3z, Knob v7.f3d]
2026-02-28 Brought in V2
    [2N7002KT7G.step, 4AxisRig.kicad_pcb, 4AxisRig.kicad_sch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]
2026-03-02 PCB V2 first draft
    [4AxisRig.kicad_pcb, 4AxisRig.kicad_sch, Download_STP_86508xx450xx+%28rev1%29.stp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]
2026-03-03 REplaced bulk caps w low esr ceramics
    [4AxisRig.kicad_pcb, driver.kicad_sch]
2026-03-03 Updated rotary encoder wiring
    [4AxisRig.kicad_pcb, 4AxisRig.step, BM04B-SRSS-TB--3DModel-STEP-1.STEP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]
2026-03-03 Updated figs
    [4AxisRig.kicad_pcb, Adafruit Grayscale 1.5-inch 128x128 OLED.brd, Adafruit Grayscale 1.5-inch 128x128 OLED.step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]
2026-03-10 Netclass Improvements
    [4AxisRig.csv, 4AxisRig.kicad_pcb, 4AxisRig.kicad_sch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]
